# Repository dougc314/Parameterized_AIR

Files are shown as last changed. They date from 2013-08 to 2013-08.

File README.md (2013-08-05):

Parameterized_AIR
=================

AIR parameterized for material width and LASER kerf.
The AIR dxf files were imported into Alibre and edited to alter various features (such as splines and blocks) 
that would not import into OpenSCAD so that they would. The final result was a DXF file that would impurt into OpenSCAD. Slots and other features (I forget for certain) were removes so that they could be added back as parameterized OpenSCAD features. The final result was an OpenSCAD file that was parameterized for material thickness and LASER kerf.

The important file is airv2_paramslots.scad. There are DXF files that get imported as well. Run this file in OpenSCAD, and set the laser kerf and material thickness appropriatly. It does take a long time to render. After rendering, export as a dxf. You will then be able to use that DXF with a laser cutter.

As the entire set of AIR parts are in OpenSCAD, they are editable. However if you are trying to alter the physical dimensions, such as printer height I believe you may have to edit the underlying DXF files.  

However you may be able cut the parts up by differencing them with flat cubes and translating the pieces.

For example

// move the top away from the bottom
translate ([as far as you would like it to get bigger])  difference () {
    import ("DXF FILE");  //the dxf file is the piece that you want to cut up and make bigger
    translate ([if necessary]) cube ([dimensioned to cut bottom of dxf file, leaving the top]);
}

([difference () {
    import ("DXF FILE");
    cube ([dimensioned to cut top of dxf file, leaving the bottom);
}    

//now you have the top seperated from the bottom, you just have to figure how to add a piece into the gap
translate ([as neseccary to fit into the gap]) cube ([dimensions of the gap])

Note that the actual thickness of the pieces don't really matter as the final step is a projection to a flat DXF. However it makes sense to use widths similiar to the material that you plan to use.

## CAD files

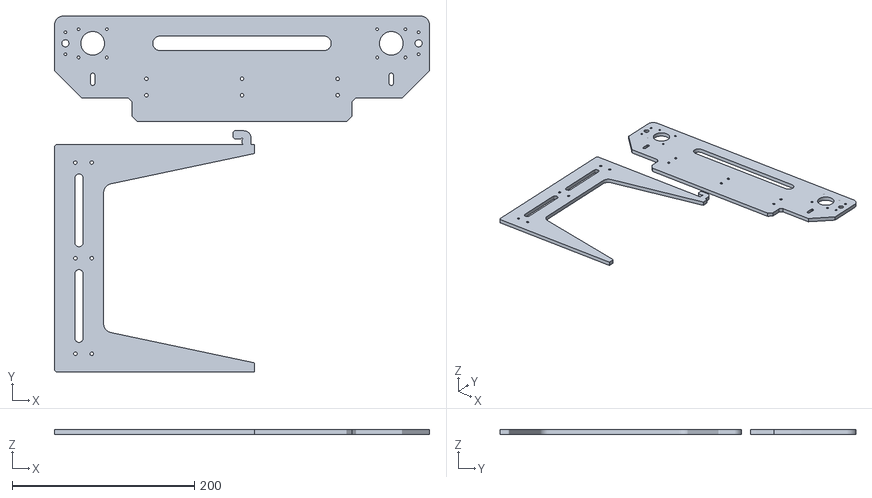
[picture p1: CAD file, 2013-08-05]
tryparam.stl
412.0 x 391.0 x 6.00

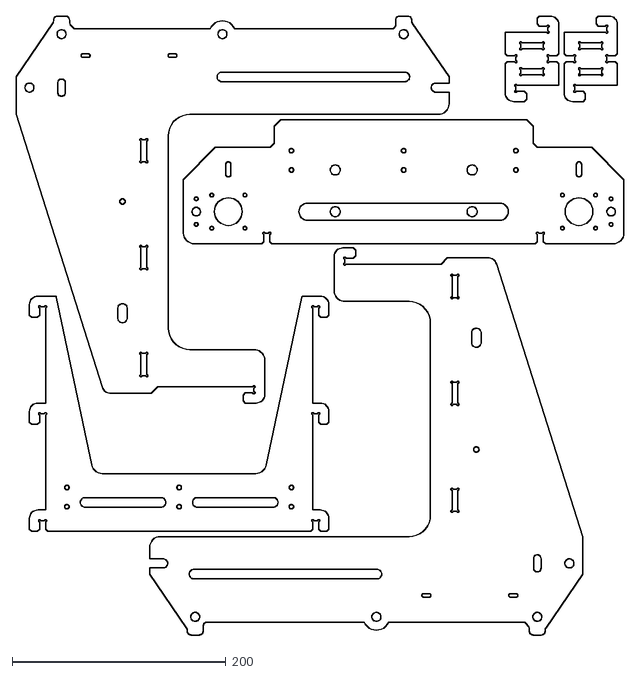
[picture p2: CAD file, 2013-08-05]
airv2_5p8_p25_2left.dxf
568.5 x 579.0

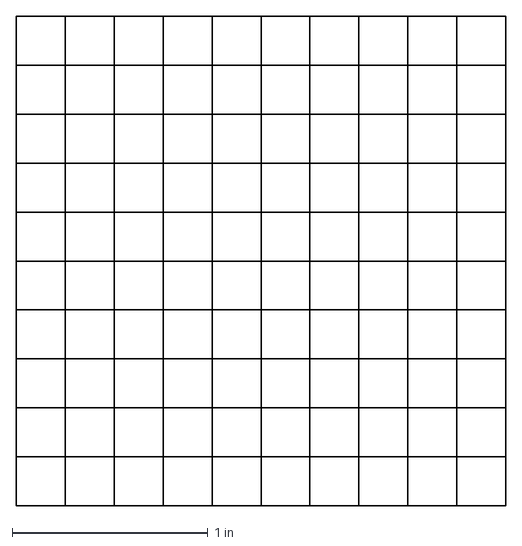
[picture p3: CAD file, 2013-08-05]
grid.dxf
2.50 x 2.50 in

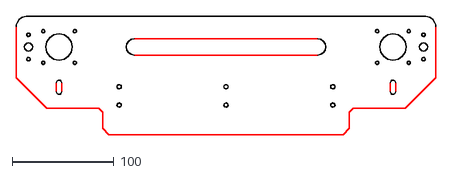
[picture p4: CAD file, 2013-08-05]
closed_top-nospline.dxf
412.0 x 116.0

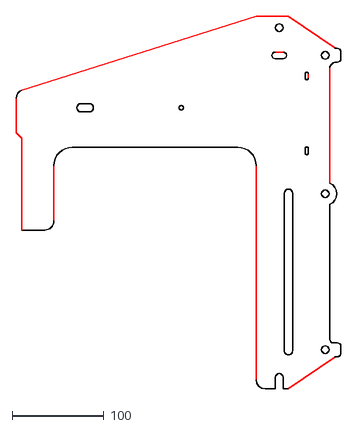
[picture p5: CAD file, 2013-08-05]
leftsideNs.dxf
353.0 x 405.0

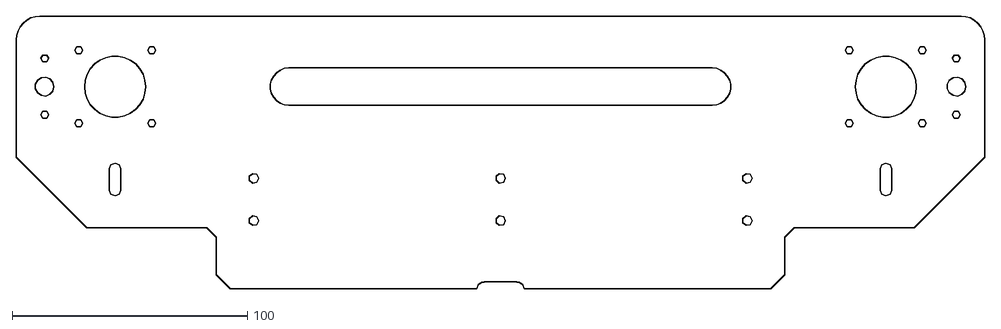
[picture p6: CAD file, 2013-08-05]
projtry.dxf
412.0 x 116.0

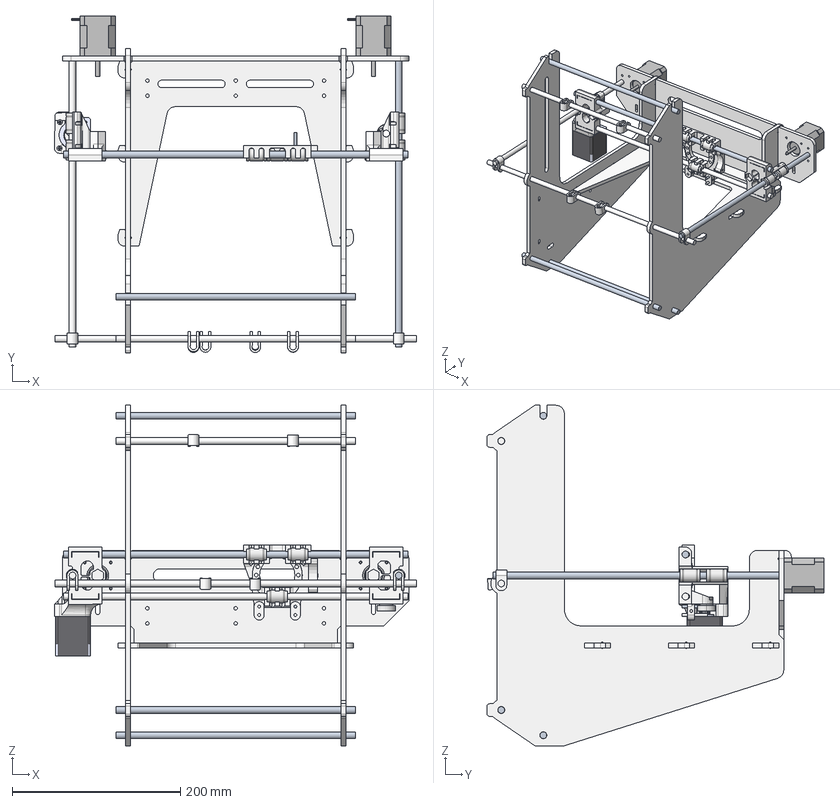
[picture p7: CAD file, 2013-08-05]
frame_v2.stp
430.6 x 400.8 x 405.0 mm

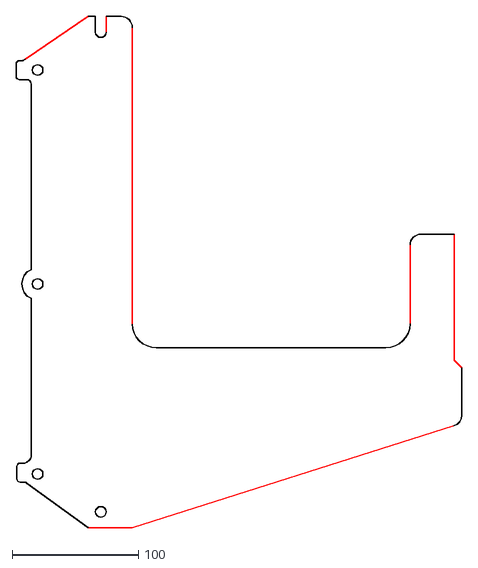
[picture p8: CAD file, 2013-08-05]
rightside_noslots.dxf
353.0 x 405.0

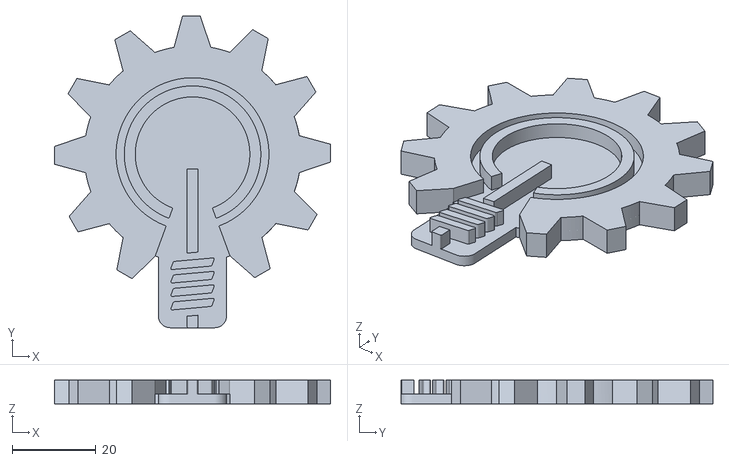
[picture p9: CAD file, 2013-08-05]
nova-labs-icon-makerbot.stl
66.0 x 74.5 x 5.66

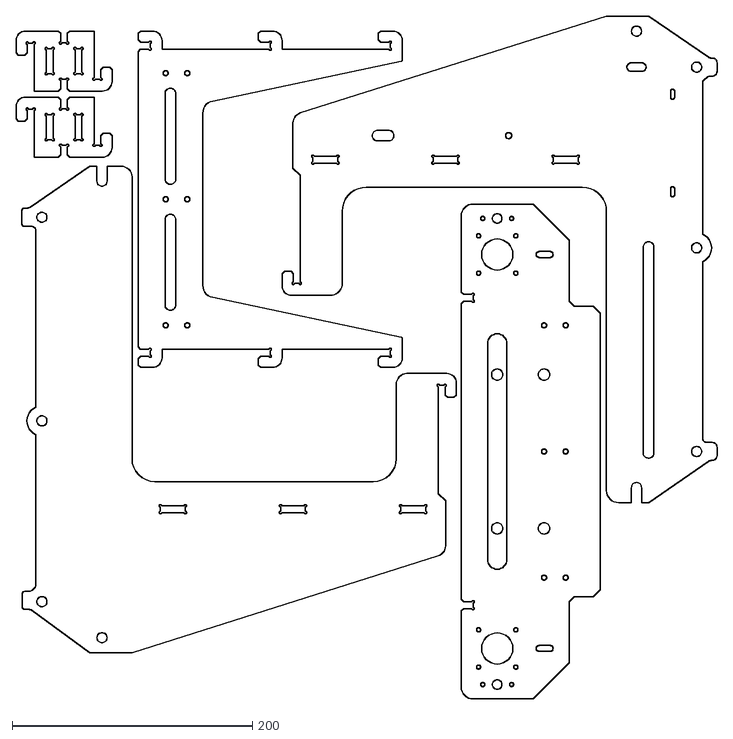
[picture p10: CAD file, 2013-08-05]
airv2_paramslots_c3.dxf
583.6 x 568.5

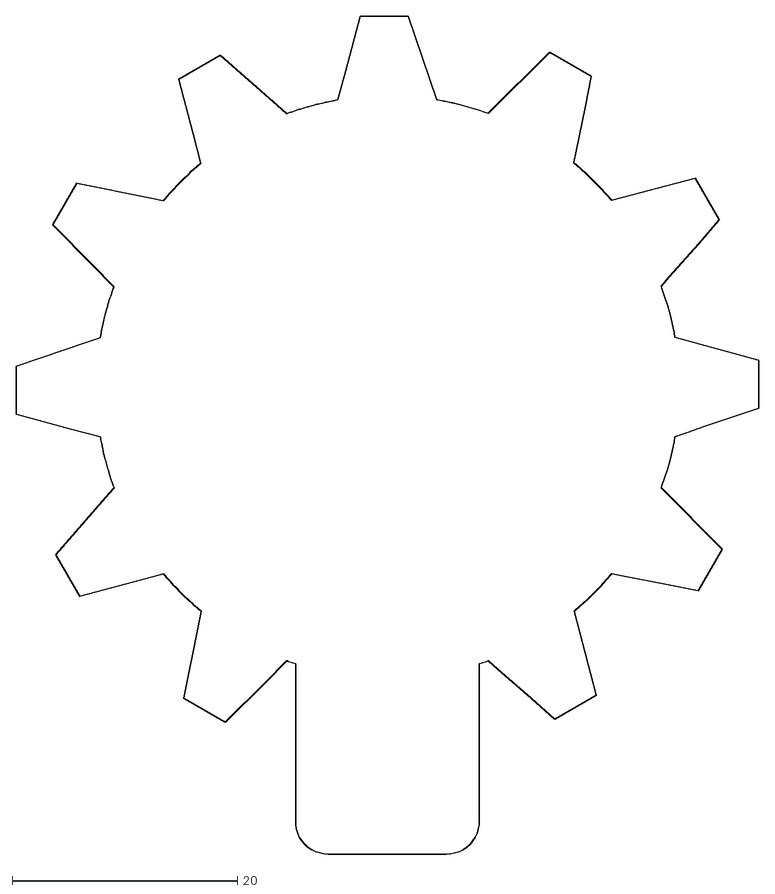
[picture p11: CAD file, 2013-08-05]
novabase.dxf
66.0 x 74.5

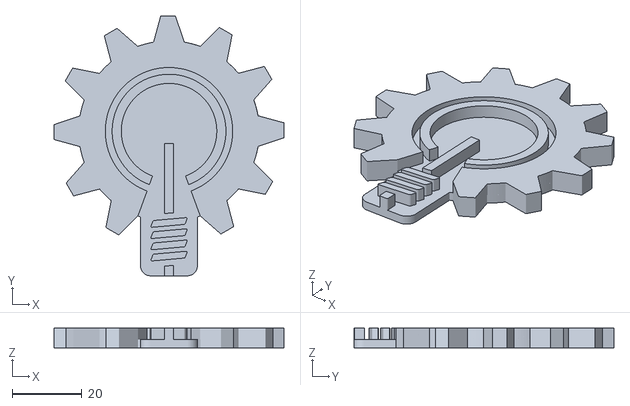
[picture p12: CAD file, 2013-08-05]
novalabsicon.stl
66.0 x 74.5 x 5.66

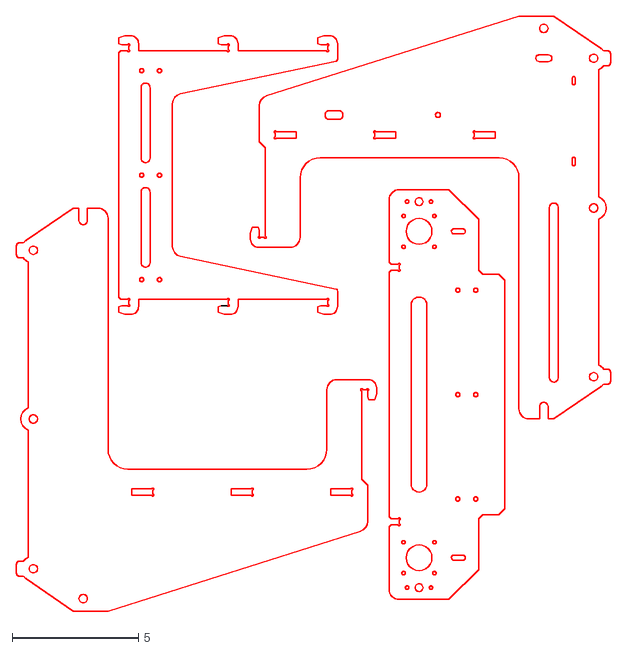
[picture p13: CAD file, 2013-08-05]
24x24xp25_1.dxf
23.5 x 23.5

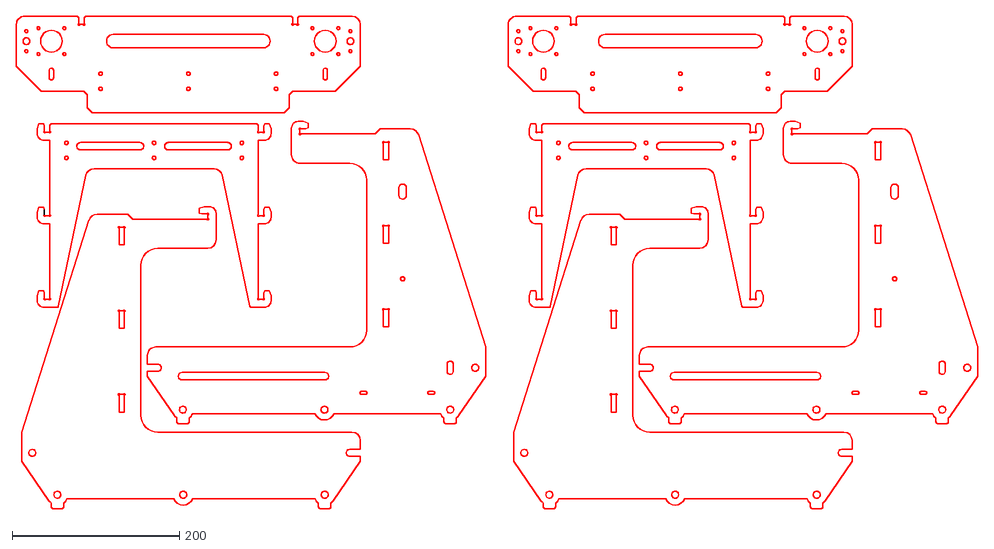
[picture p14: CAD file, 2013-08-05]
2x4_2aircut_p250.dxf
1151.1 x 590.1

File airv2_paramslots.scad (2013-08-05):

// AIR ver 2 parametric only for material thickness and laser kerf 

//added holes for a handle

$fn=32;
// build group 3 settings
material_thk = 5.8;
laser_kerf = 0.25;
correction = 0;

   
%translate ([-24*25.4,0,0]) cube ([24*25.4,24*25.4,.01],center=false); //test plate size
//bounds () ;  //id the 4 corners 
plate ();

module plate () {

  translate ([-120,-75+304.8,0]) rotate ([0,0,90]) {

    airv2 (material_thk,laser_kerf,correction);  //comment this line out to just cut a test coupon
    test2 (material_thk,laser_kerf,correction,4); //0 is off, 1,2,3,4  or 5 are various unused spaces 4 is lower right

  }
}



module bounds () {
  projection (cut = true) {
  for (i=[-1,1])
  for (k=[-1,1])
    translate ([(12*25.4-1)*i,(12*25.1-1)*k,0]) cube ([1,1,1],center=true);
  
  }
}

module test2 (mat,kerf,fudge,area) {
  projection (cut = true) {
    if (area == 1) {
       translate ([-300,25,0])  testcoupon (mat,kerf,fudge);
       translate ([-240,25,0])  testcoupon (mat,kerf,fudge);
    } else if (area == 2) {
         translate ([-285,250,0])  testcoupon (mat,kerf,fudge);
         translate ([-285,175,0])  testcoupon (mat,kerf,fudge);
    } else if (area == 3) {
         translate ([-436.6,325,0])  rotate ([0,0,90]) testcoupon (mat,kerf,fudge);
         translate ([-436.6,270,0]) rotate ([0,0,90])  testcoupon (mat,kerf,fudge);
    } else if (area == 4) {
         translate ([67,-120,0]) rotate ([0,0,90]) testcoupon (mat,kerf,fudge);
         translate ([67,-175,0]) rotate ([0,0,90]) testcoupon (mat,kerf,fudge); 
      } else if (area == 5) {
         translate ([-155,185,0]) rotate ([0,0,90]) testcoupon (mat,kerf,fudge);
         translate ([-155,130,0]) rotate ([0,0,90]) testcoupon (mat,kerf,fudge); 
      } else {}
 }  
}



module airv2 (mat,kerf,fudge) {
projection(cut = true) { 
   translate ([10,0,0]) rotate ([0,0,90])  top(mat,kerf,fudge);
   translate ([-375,210,0]) rotate ([0,0,90]) bracket (mat,kerf,fudge);
    translate ([-240,130,0]) leftside (mat,kerf,fudge);
    translate ([-125,65,0])  rotate ([0,0,180]) rightside(mat,kerf,fudge);
    //translate ([-125,65,0])  rotate ([0,0,180]) leftside(mat,kerf,fudge);


  }

}

module testcoupon (mat,kerf,fudge) {
  wid = mat-kerf+fudge;
  relieve_r=1;
  difference () {
    union () {
      cube ([50,50,mat],center=true);
      translate ([15,25,0])  rotate ([0,0,90]) mirror ([0,0,0]) hooked_slot (wid,10,2,mat,relieve_r,true); 
      translate ([-15,-25,0])  rotate ([0,0,-90]) mirror ([0,0,0]) hooked_slot (wid,10,2,mat,relieve_r,true);   
    }
    union () {
     translate ([0,12,0]) rotate ([0,0,90]) closed_slot (wid,21-kerf/2,mat,1,true);
    translate ([0,-12,0]) rotate ([0,0,90]) closed_slot (wid,21-kerf/2,mat,1,true);
     translate ([-25.01,0,0]) rotate ([0,0,-90]) open_slot (wid,10-kerf/2,2,mat,1,true);
      translate ([25.01,0,0]) rotate ([0,0,90]) open_slot (wid,10-kerf/2,2,mat,1,true);     

     translate ([15,25,0]) cylinder (r1=relieve_r,r2=relieve_r,h=mat,center=true);
     translate ([-15,-25,0]) cylinder (r1=relieve_r,r2=relieve_r,h=mat,center=true);
    }
  }

}

module leftside (mat,kerf,fudge) {
  wid = mat-kerf+fudge;
  relieve_r=1;
  difference () {
    union () {
      linear_extrude(file = "leftsidens.dxf",  height = mat,center=true);
      // rotate ([180,180,0]) linear_extrude(file = "rightsidens.dxf",  height = mat,center=true);

       translate ([0,10,0])  rotate ([0,0,0]) mirror ([1,0,0]) hooked_slot (wid,10,2,mat,relieve_r,true);      
     }
     union() {
        for (i=[0,1,2]) {
          translate ([21+i*100,113,0]) rotate ([0,0,90]) closed_slot (wid,21-kerf,mat,relieve_r,true);
        }
        translate ([0,10,0]) cylinder (r1=relieve_r,r2=relieve_r,h=mat,center=true);
     }
   }
}



module rightside (mat,kerf,fudge) {
  wid = mat-kerf+fudge;
  relieve_r=1;
  difference () {
    union () {
     // linear_extrude(file = "leftsidens.dxf",  height = mat,center=true);
      rotate ([180,180,0]) linear_extrude(file = "rightsidens.dxf",  height = mat,center=true);

       translate ([0,10,0])  rotate ([0,0,0]) mirror ([1,0,0]) hooked_slot (wid,10,2,mat,relieve_r,true);      
     }
     union() {
        for (i=[0,1,2]) {
          translate ([21+i*100,113,0]) rotate ([0,0,90]) closed_slot (wid,21-kerf,mat,relieve_r,true);
        }
        translate ([0,10,0]) cylinder (r1=relieve_r,r2=relieve_r,h=mat,center=true);        
     }
   }
}




module bracket (mat,kerf,fudge) {
  wid = mat-kerf+fudge;
  relieve_r=1;
  difference () {
    union () {
      linear_extrude(file = "bracket_closed.dxf",  height = mat,center=true);
      for (i = [-2,-1,0]) {
        translate ([125,i*100-10,0])  rotate ([0,0,0]) hooked_slot (wid,10-kerf/2,2,mat,relieve_r,true);
        translate ([-125,i*100-10,0])  rotate ([0,0,0]) mirror ([1,0,0]) hooked_slot (wid,10-kerf/2,2,mat,relieve_r,true);
      }
     }
   union() {
       for (i = [-2,-1,0]) {
      translate ([125,i*100-10,0])  cylinder (r1=1,r2=relieve_r,h=mat,center=true);
      translate ([-125,i*100-10,0])   cylinder (r1=1,r2=relieve_r,h=mat,center=true);
    }
   }
  }
}

module top(mat,kerf,fudge) {
  wid = mat-kerf+fudge;
difference () {
    union () {
      linear_extrude(file = "closed_top-nospline.dxf",  height = mat,center=true);
        translate ([-64,86,0]) cylinder (r1=4.7,r2=4.7, h=mat+.01, center=true);
        translate ([64,86,0]) cylinder (r1=4.7,r2=4.7, h=mat+.01, center=true);
    }
    union () {
      translate ([-127.95,116,0]) mirror ([0,1,0]) open_slot (wid,10-kerf/2,2,mat,1,true);
      translate ([127.95,116,0]) mirror ([0,1,0]) open_slot (wid,10-kerf/2,2,mat,1,true);
    #translate ([-64,47,0]) cylinder (r1=4.7,r2=4.7, h=mat+.01, center=true);
    translate ([64,47,0]) cylinder (r1=4.7,r2=4.7, h=mat+.01, center=true);


    }
  }
}

module hooked_slot (x,y,bev,thk,r,relieve) {
  difference () {
     union () {
        linear_extrude (height=thk,center=true) 
          polygon ([[0,0],[x,0],[x,y-bev],[x+bev,y],[15-bev,y],[15,y-bev],[15,-2],[0,-2]]);
        translate ([3.5,-6,0]) cube ([7,8,thk],center=true);    
        intersection () {
          translate ([7.5,-6,0]) cube ([15,8,thk],center=true);
          translate ([7,-2,0]) cylinder (r1=8,r2=8,h=thk,center=true); 
        }
      }
    if (relieve==true) {
      //cylinder (r1=r,r2=r,h=thk,center=true); //can't do tihe here it has do cut the abutting object too
      translate ([x,0,0])  cylinder (r1=r,r2=r,h=thk,center=true);
    }
  }
}

  
module closed_slot (x,y,thk,r,relieve) {
  union ()
{ linear_extrude (height=thk,center=true) polygon ([[-x/2,y/2],[-x/2,-y/2],[x/2,-y/2],[x/2,y/2]]);
 if (relieve==true)
  { translate ([-x/2,y/2]) cylinder (r1=r,r2=r,h=thk,center=true);
     translate ([x/2,y/2]) cylinder (r1=r,r2=r,h=thk,center=true);
     translate ([-x/2,-y/2]) cylinder (r1=r,r2=r,h=thk,center=true);
     translate ([x/2,-y/2]) cylinder (r1=r,r2=r,h=thk,center=true);
  } 
  }

}
module open_slot (x,y,bev,thk,r,relieve) {
  union ()
{ linear_extrude (height=thk,center=true) polygon ([[-x/2-bev,0],[-x/2,bev*sign(y)],[-x/2,y],[x/2,y],[x/2,bev*sign(y)],[x/2+bev,0]]);
 if (relieve==true)
  { translate ([-x/2,y]) cylinder (r1=r,r2=r,h=thk,center=true);
     translate ([x/2,y]) cylinder (r1=r,r2=r,h=thk,center=true);
  } 
  }

}


module roundslot (L,W,H) {
  sep = L-W;
  translate ([-sep/2,0,0]) cylinder (r=W/2,h=H,center=true);
  translate ([sep/2,0,0]) cylinder (r=W/2,h=H,center=true);  		
  cube ([sep,W,H],center=true);
}

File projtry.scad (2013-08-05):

  import_stl ("tryparam.stl");

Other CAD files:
AIRV2-3Dmodel_step203.stp
225x225.dxf
closed_top-nospline_bad.dxf
novatop.dxf
tryparam.scad
tryparam_hook.scad
24x36xp25_2b.dxf
24x36xp25_2s.dxf
24x36xp25_2t.dxf
AIRV2-3Dmodel.FCStd
aircoupon_hdacrylic.dxf
airv2_5p8_p25_left_right.dxf
airv2_paramslots.dxf
airv2_paramslots_c4.dxf
bracket_closed.dxf
bracket_nospline_closed.dxf
bracket_top.dxf
closed_top.dxf
closed_top_left.dxf
closedtopleft.dxf
open_top-nospline.dxf
open_top.dxf
rightsidens.dxf
simpletest.dxf
top_dimensioned.dxf
toptry.scad
trylogo.scad
xcarriage.stl
ybeltclamp-tenadj.stl

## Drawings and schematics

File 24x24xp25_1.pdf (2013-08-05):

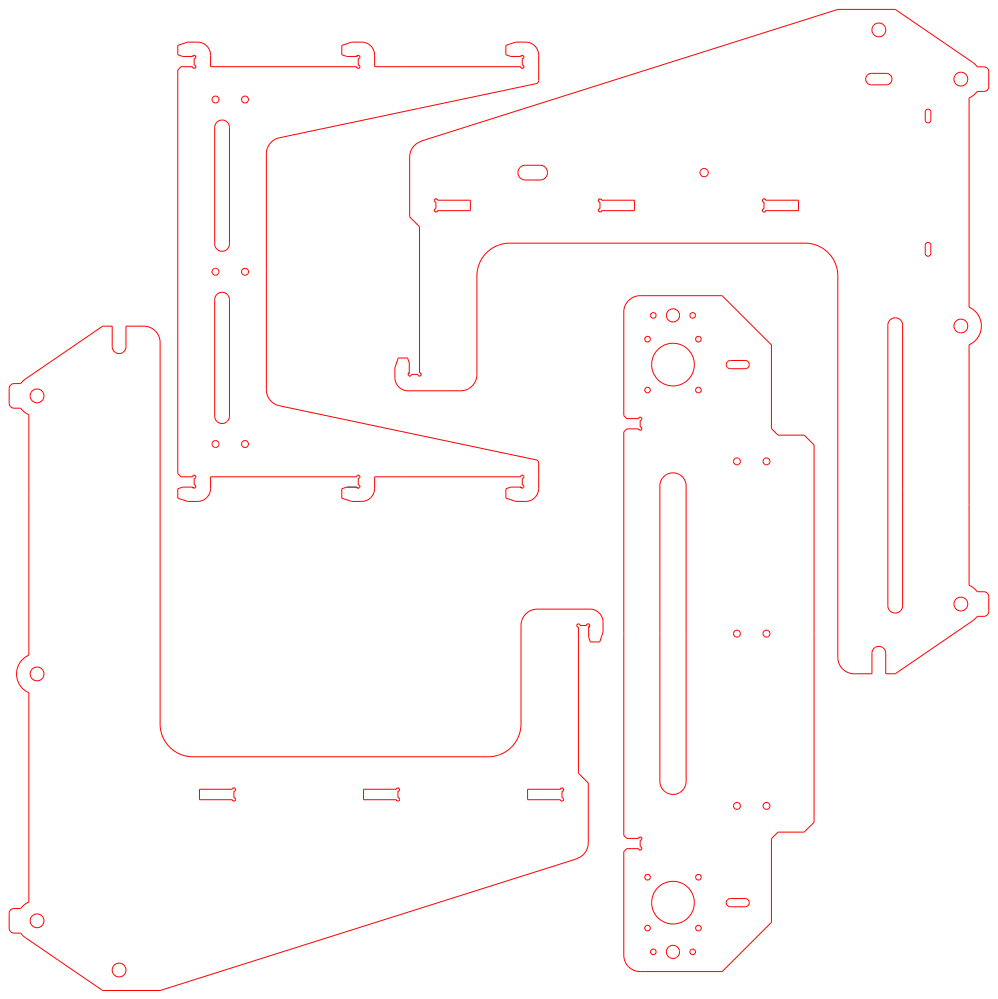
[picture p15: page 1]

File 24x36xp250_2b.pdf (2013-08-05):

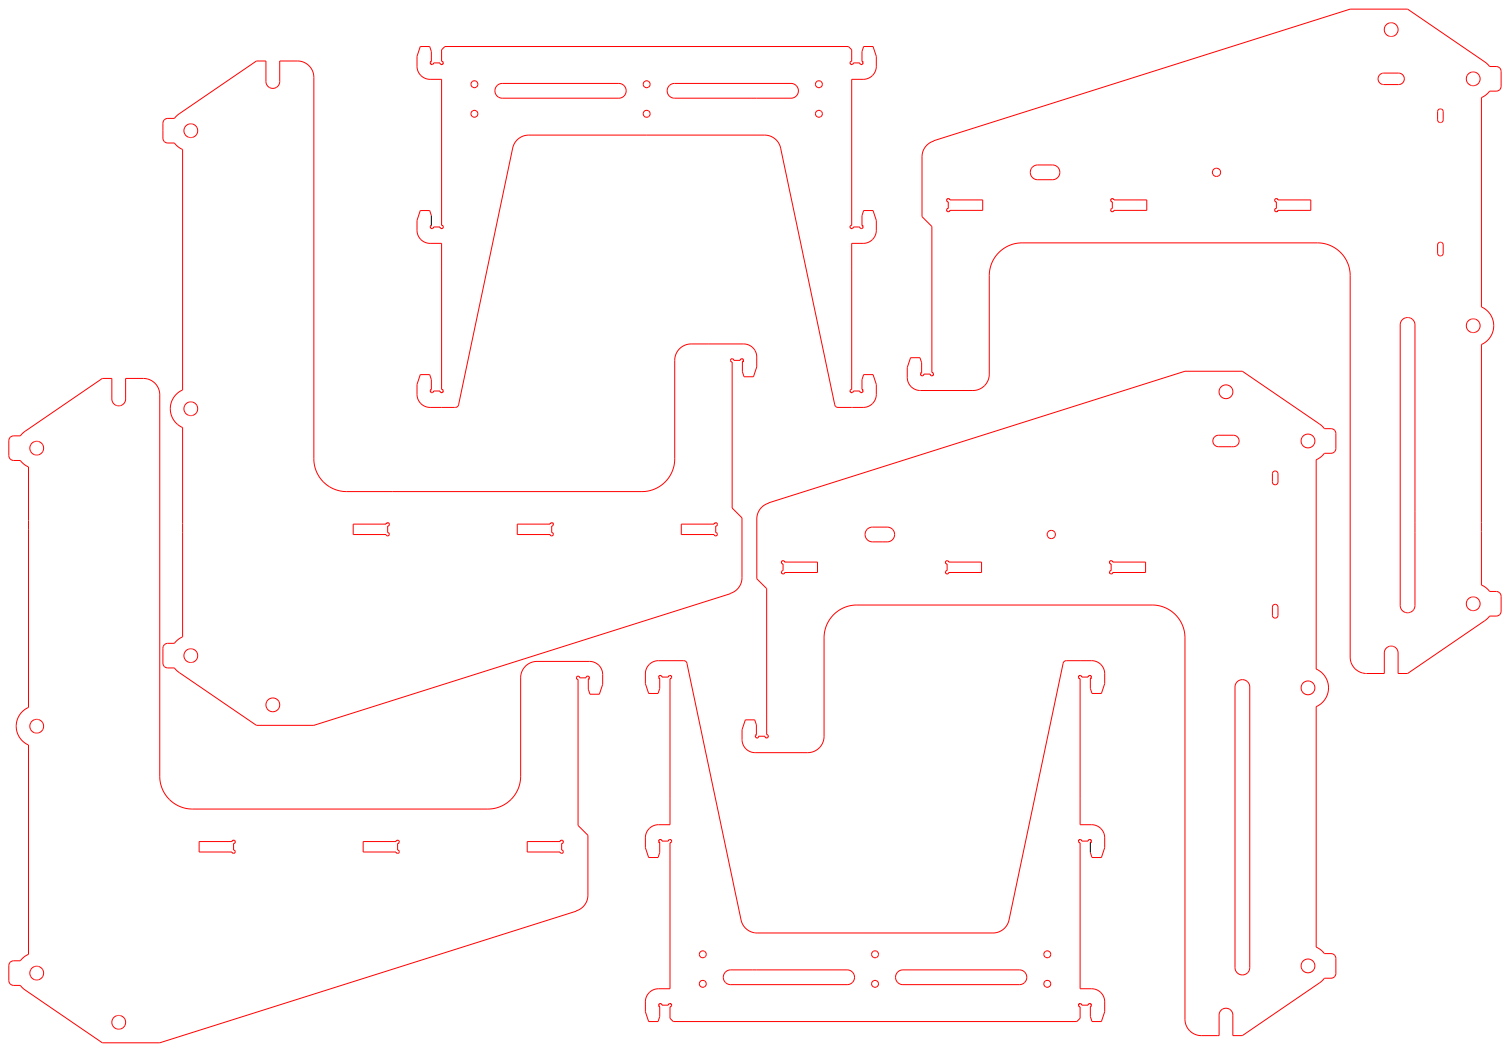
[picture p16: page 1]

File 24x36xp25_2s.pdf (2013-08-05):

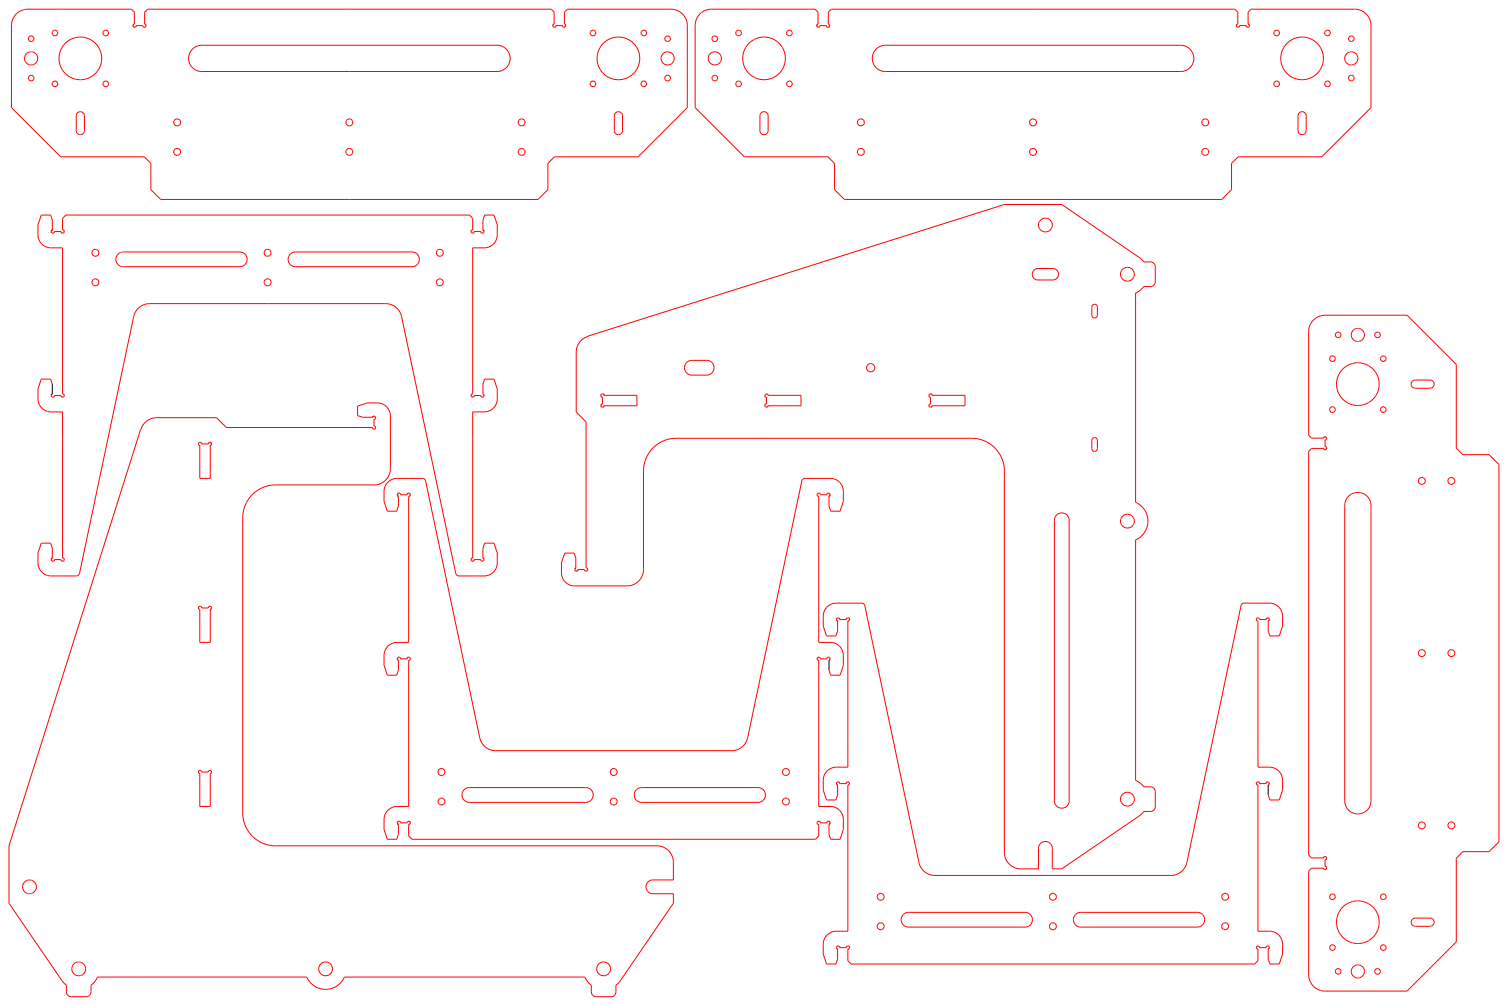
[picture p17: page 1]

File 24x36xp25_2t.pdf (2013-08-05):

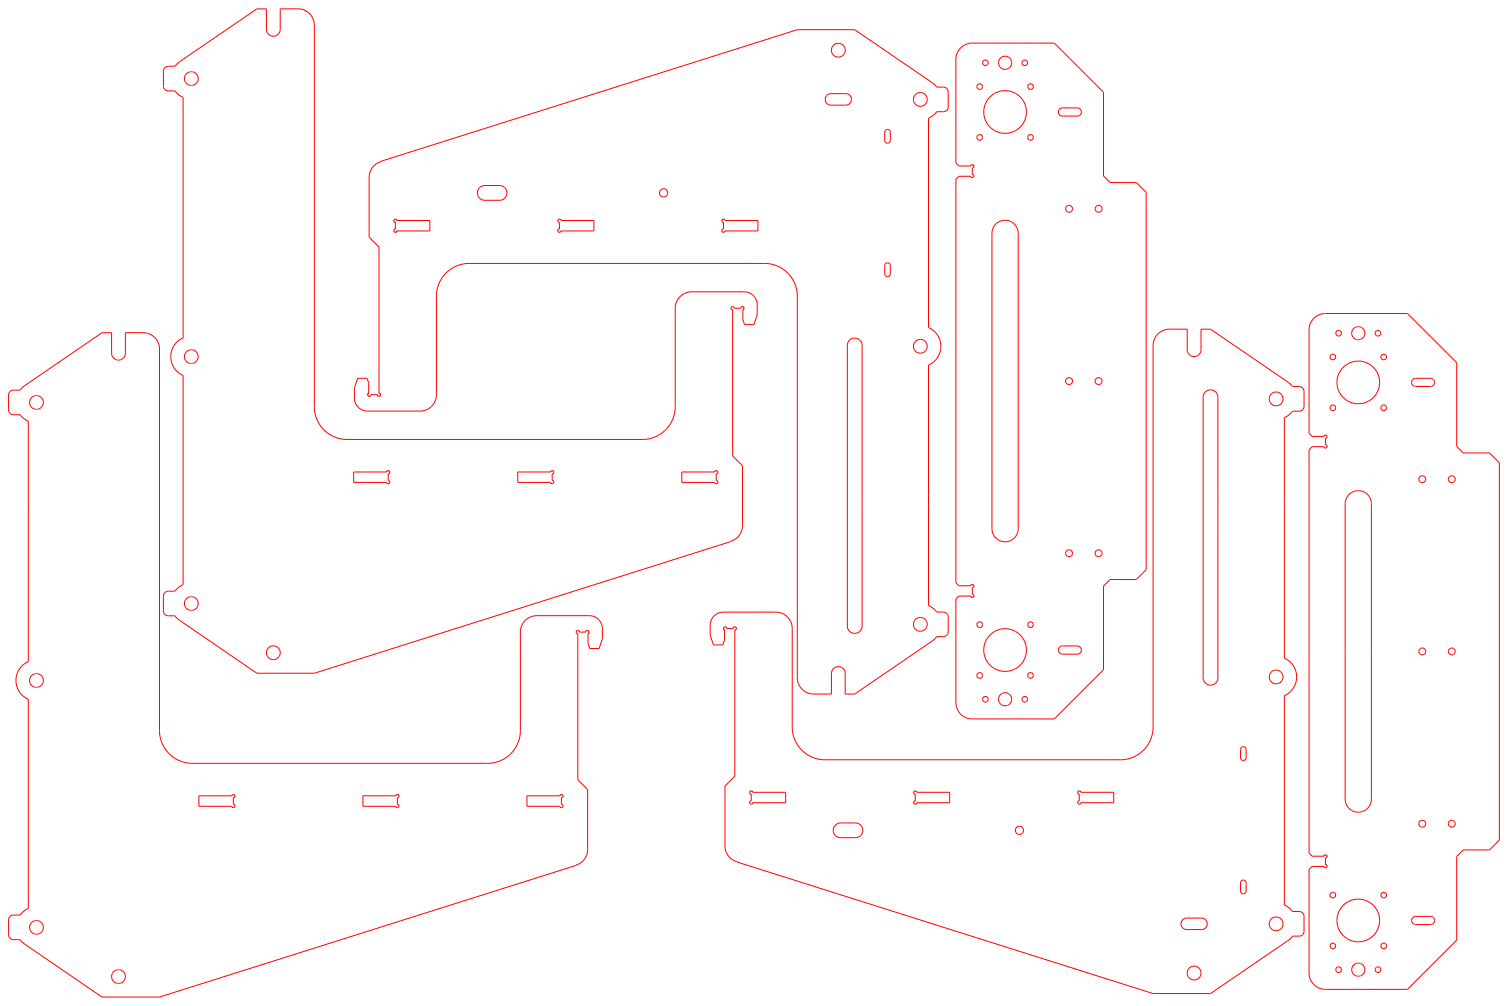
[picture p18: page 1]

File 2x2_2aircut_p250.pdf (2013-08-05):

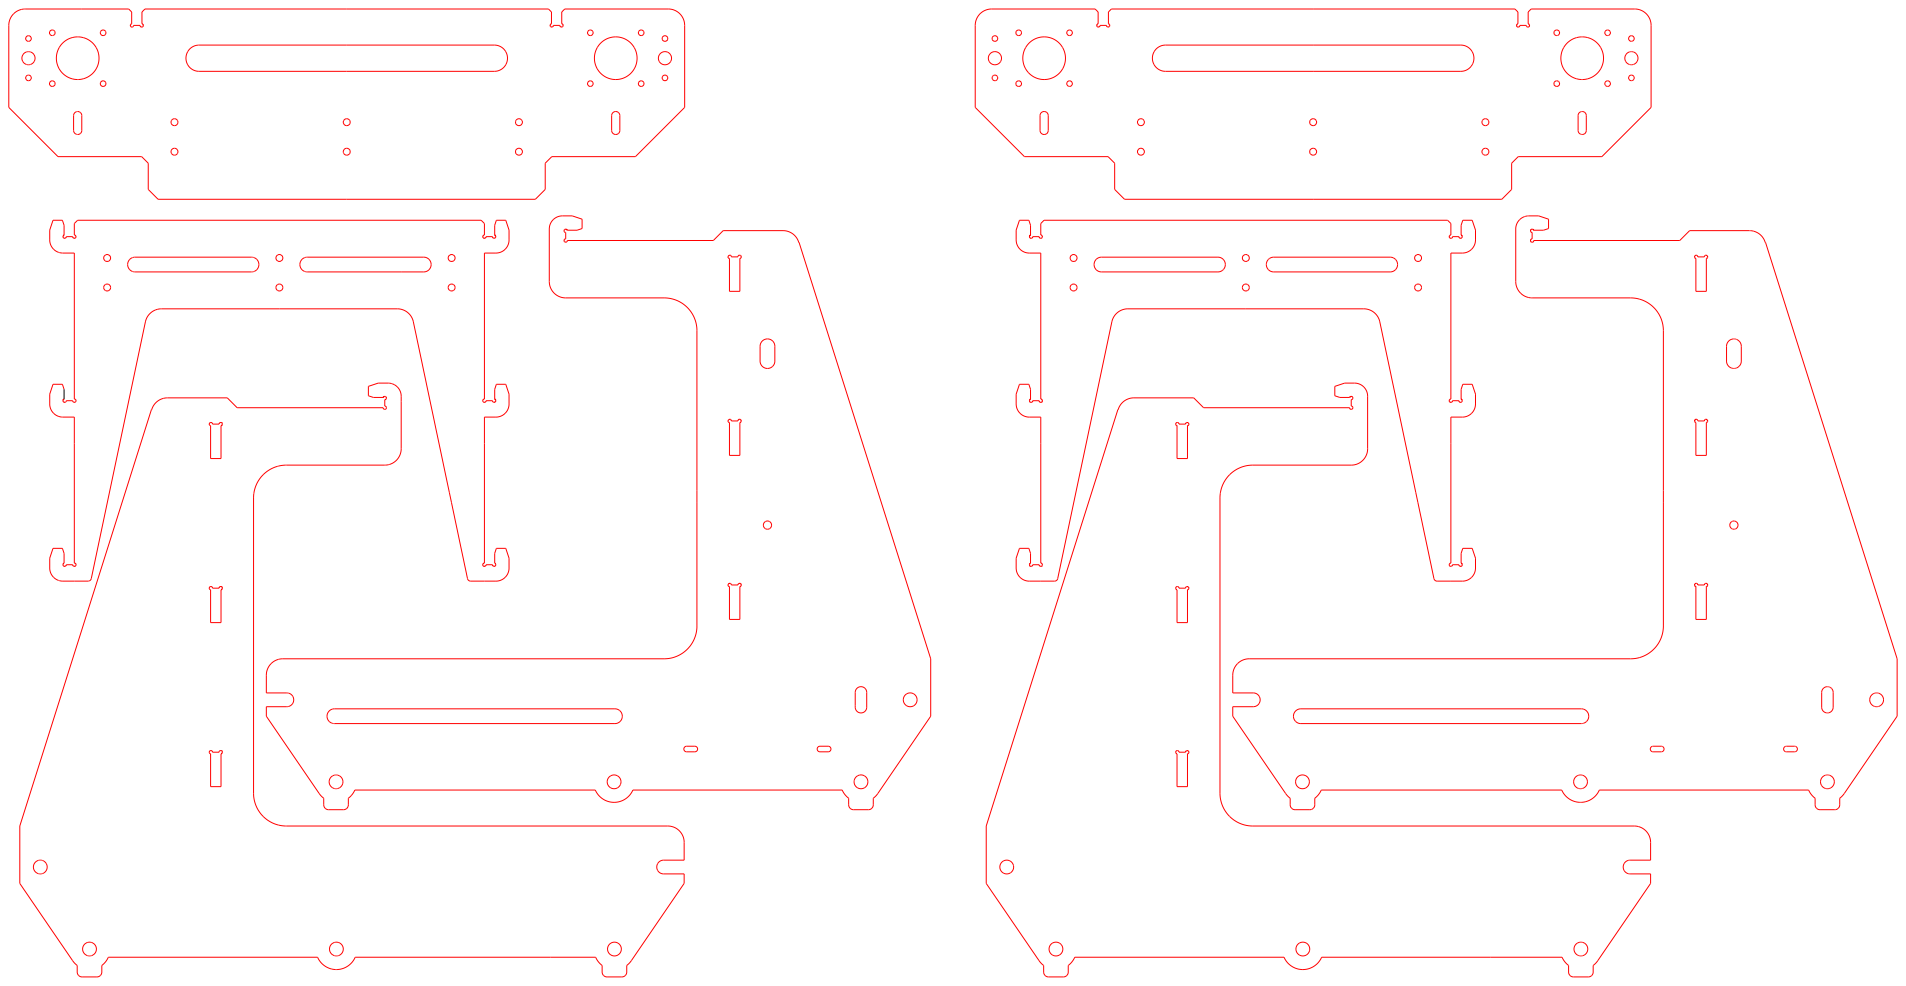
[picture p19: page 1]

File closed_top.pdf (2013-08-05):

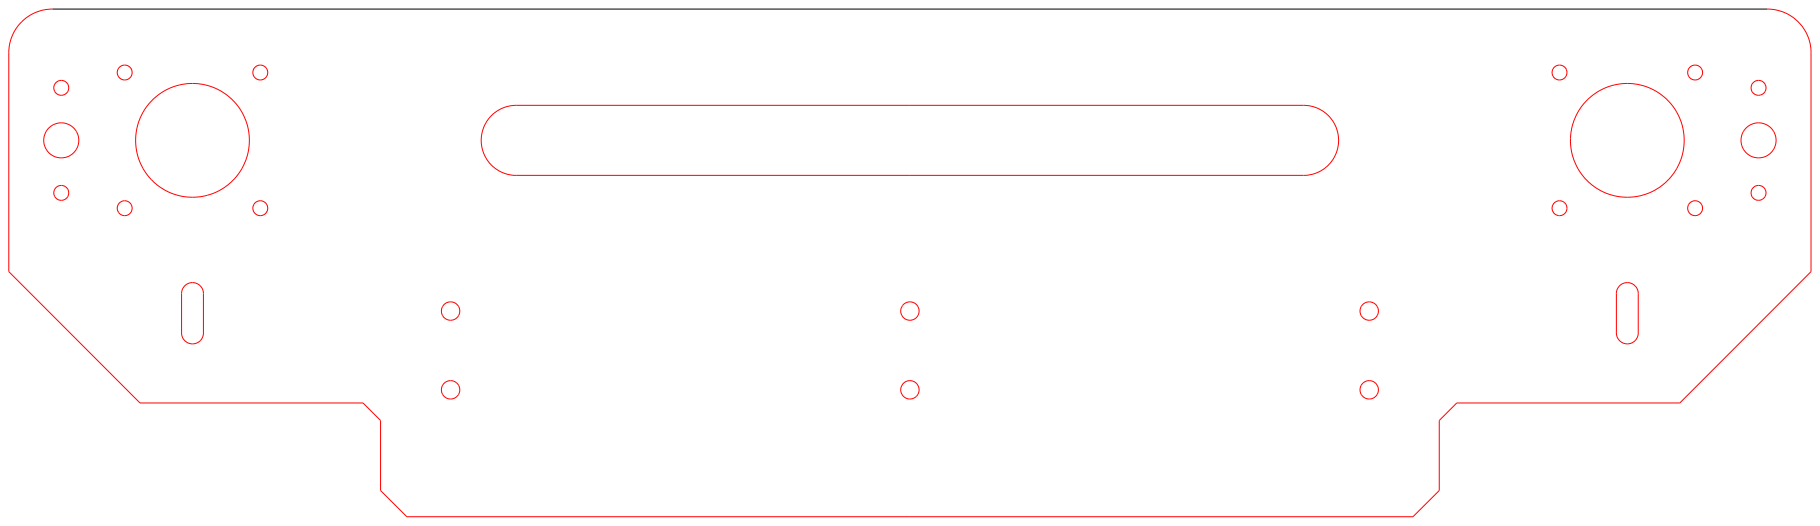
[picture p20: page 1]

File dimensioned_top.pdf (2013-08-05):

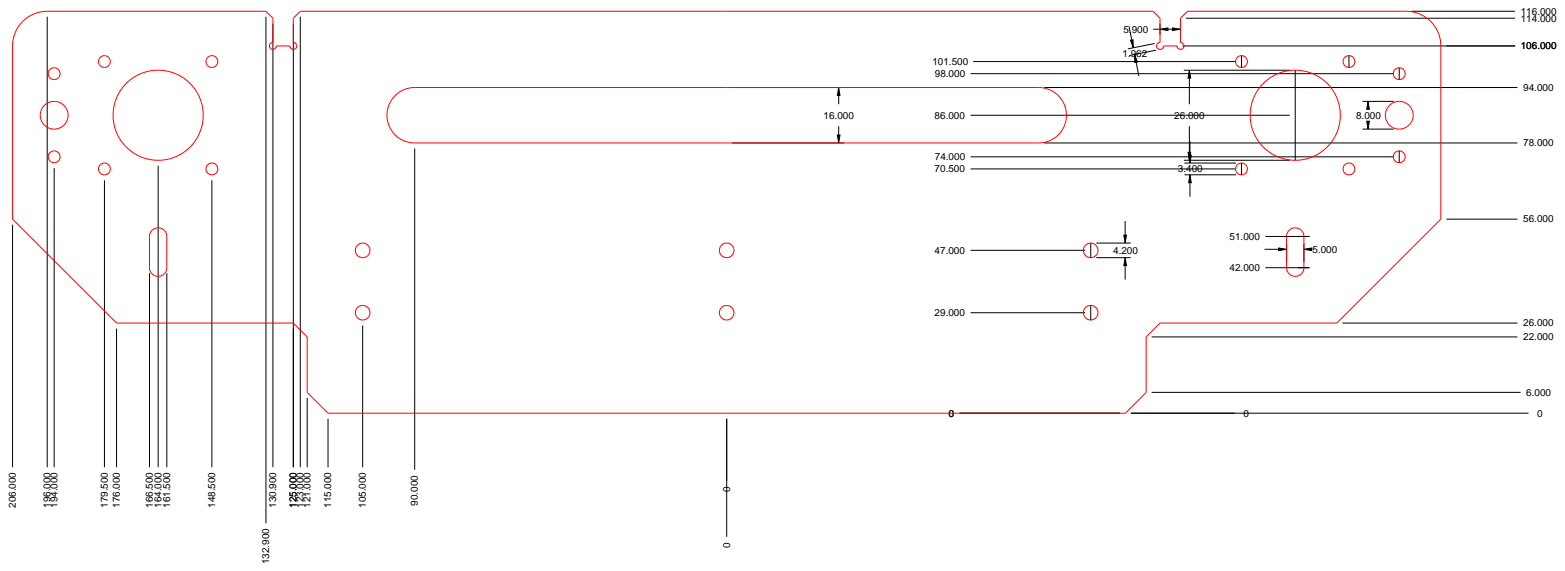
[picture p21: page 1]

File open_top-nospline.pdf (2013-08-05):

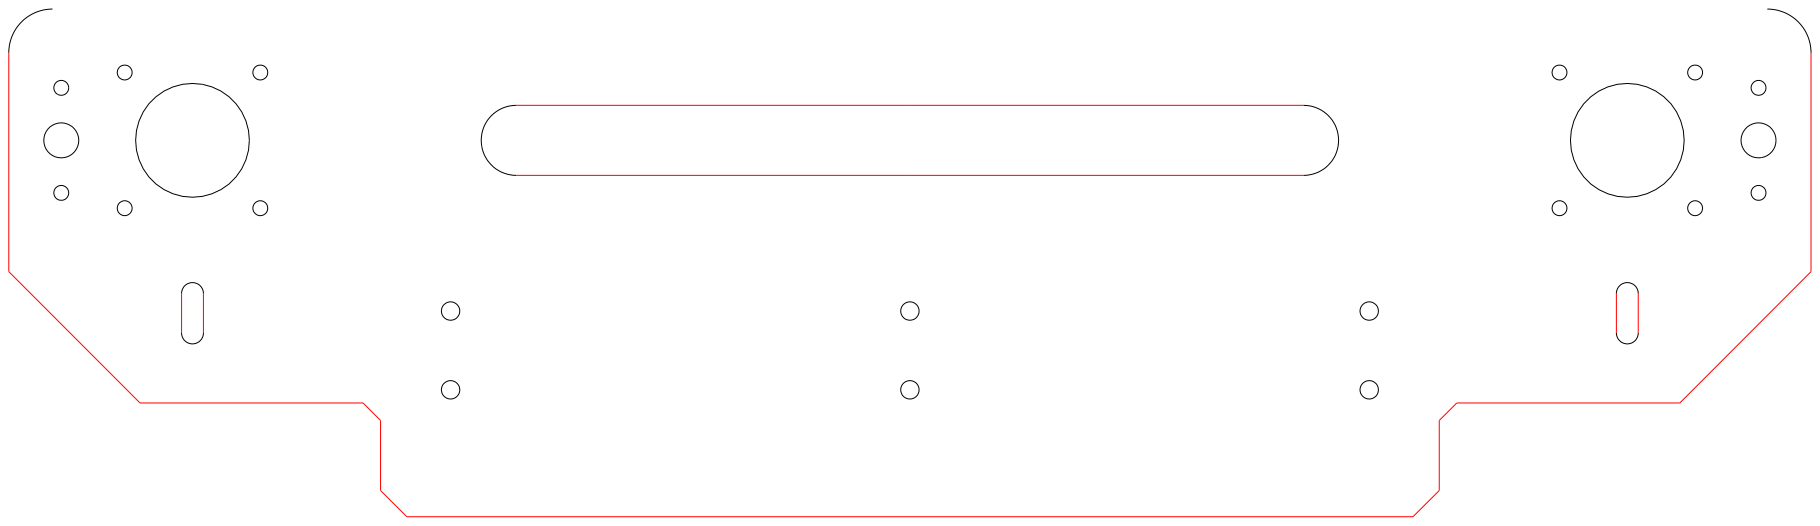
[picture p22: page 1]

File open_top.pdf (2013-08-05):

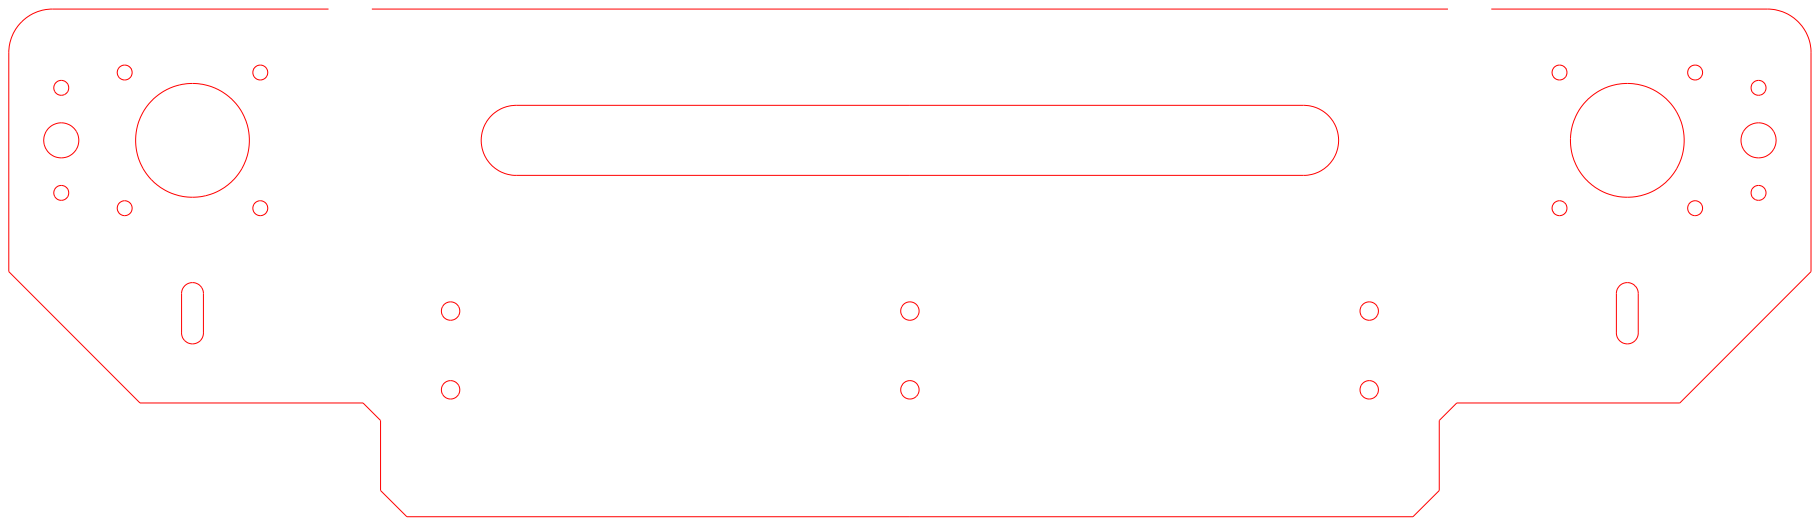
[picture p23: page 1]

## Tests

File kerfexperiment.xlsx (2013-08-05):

Quarter inch cubies |  |  | one inch square with notches
bigger | smaller |  | bigger | smaller | notches
0.231 | 0.227 |  |  |  | width | center mass
0.231 | 0.226 |  | 0.977 | 0.973 | 0.219 | 0.38 | 0.379
0.229 | 0.226 |  |  |  | 0.22
0.23 | 0.226 |  |  |  | 0.22
0.231 | 0.226 |  |  |  | 0.219
0.23 | 0.227
0.23 | 0.229 |  | 0.98 | 0.976 | 0.219 | 0.382 | 0.382
0.234 | 0.23 |  |  |  | 0.218
0.231 | 0.229 |  |  |  | 0.22
0.232 | 0.23 |  |  |  | 0.22
0.23 | 0.227
0.23 | 0.229
0.23 | 0.229
0.239 | 0.229
0.229 | 0.216
0.231 | 0.227
0.234 | 0.227
0.2312941176 | 0.2270588235 | avg | 0.9785 | 0.9745 | 0.219375 | 0.381 | 0.3805
0.002443478716 | 0.003191210355 | standard deviation
0.25 | 0.25 |  | 1 | 1 | 0.22 | 0.4 | 0.4
0.01870588235 | 0.02294117647 |  | 0.0215 | 0.0255 | 0.000625 | 0.019 | 0.0195 | laser kerf based on each set of measurements
 |  |  |  |  |  | -0.0025 | -0.006 | expectation based on smaller square
